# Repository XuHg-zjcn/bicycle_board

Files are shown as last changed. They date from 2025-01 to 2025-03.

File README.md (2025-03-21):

# 自行车主控板

## 前系统特征
### 板载资源
- ESP32-C3-WROOM-2U, xx32F103C8T6
- 太阳能Buck降压电路，可用MPPT驱动
- USB 5V输出升压电路(PS7516)
- USB充电电路(TP4056)
- 数字功放(NS4168)
- 2路NMOS(可连接车灯、报警器)
- IMU传感器(QMI8610,ICM-42688-P)
- 磁力计(QMC6308,QMC7983)
- 气压计(SPL06-001)
- 温湿度计(AHT20)
- FRAM储存器(MB85RS256B)

### 接口
- 8PIN SPI显示屏接口
- 扬声器接口
- I2S麦克风
- TF卡槽
- 3.7V锂电池接口
- 外置I2C接口(连接传感器和GPIO扩展芯片)
- 指纹传感器接口
- 后系统接口(UART)
- USB-C口(可充电,连接ESP32-C3模块)
- USB-A口(可放电,连接xx32芯片)
- 5V输出接口，用于连接USB公头
- 霍尔传感器接口x2(2个可以用于区分前进和后退)

### 待添加
- USB PD输出
- 外置电池组接口
- 转向角编码器接口
- 板载LoRa模块
- 发电机稳压电路

## 评论
前系统有一些射频发射源，GNSS模块和天线打算放在后系统附近，通过增大距离来减少干扰。  
暂时不考虑刷卡解锁，先考虑支持指纹和蓝牙  
按键，刹车开关，副车灯，风扇等电路等放在与显示屏同一块PCB中，使用PCA9555/TCA9555 GPIO扩展芯片  
为了提高稳定性，IMU和磁力计PCB上各有两个的不同封装可以焊接，只焊一个也可以。

为了减少git仓库占用空间，我在`git commit`提交前在KiCad中清除所有填充域(快捷键Ctrl+B)，您可以在打开后重新填充(快捷键B)  
在KiCad的Python控制台中，切换到该repo根目录运行下例命令
````python
import build
build.all()
```
即可自动完成添加泪滴、重新填充、应用PCB背面信息字符串

## 历史
2024.12.23 发布v1.0(第一次PCB打样)

下一个版本考虑
- 把ESP32和外围设备(microSD、音频等)等移动到显示屏附近PCB上
- 是否应该将太阳能、发电机相关电路尽可能移动到太阳能板、发电机附近

2025.2.21 发现TXB0108PW的OE端未连接，已飞线连接到+1V8

2025.3.21 发现用于光伏MPPT的DCDC不可用，Q6栅极关闭时电流会从体二极管流过

## 版权和许可证
Copyright (C) 2024 徐瑞骏

本设计以CERN开放硬件许可证第二版强互惠授权(CERN Open Hardware Licence Version 2 - Strongly Reciprocal)，许可证文件位于`LICENSE.txt`

本设计不提供任何保证

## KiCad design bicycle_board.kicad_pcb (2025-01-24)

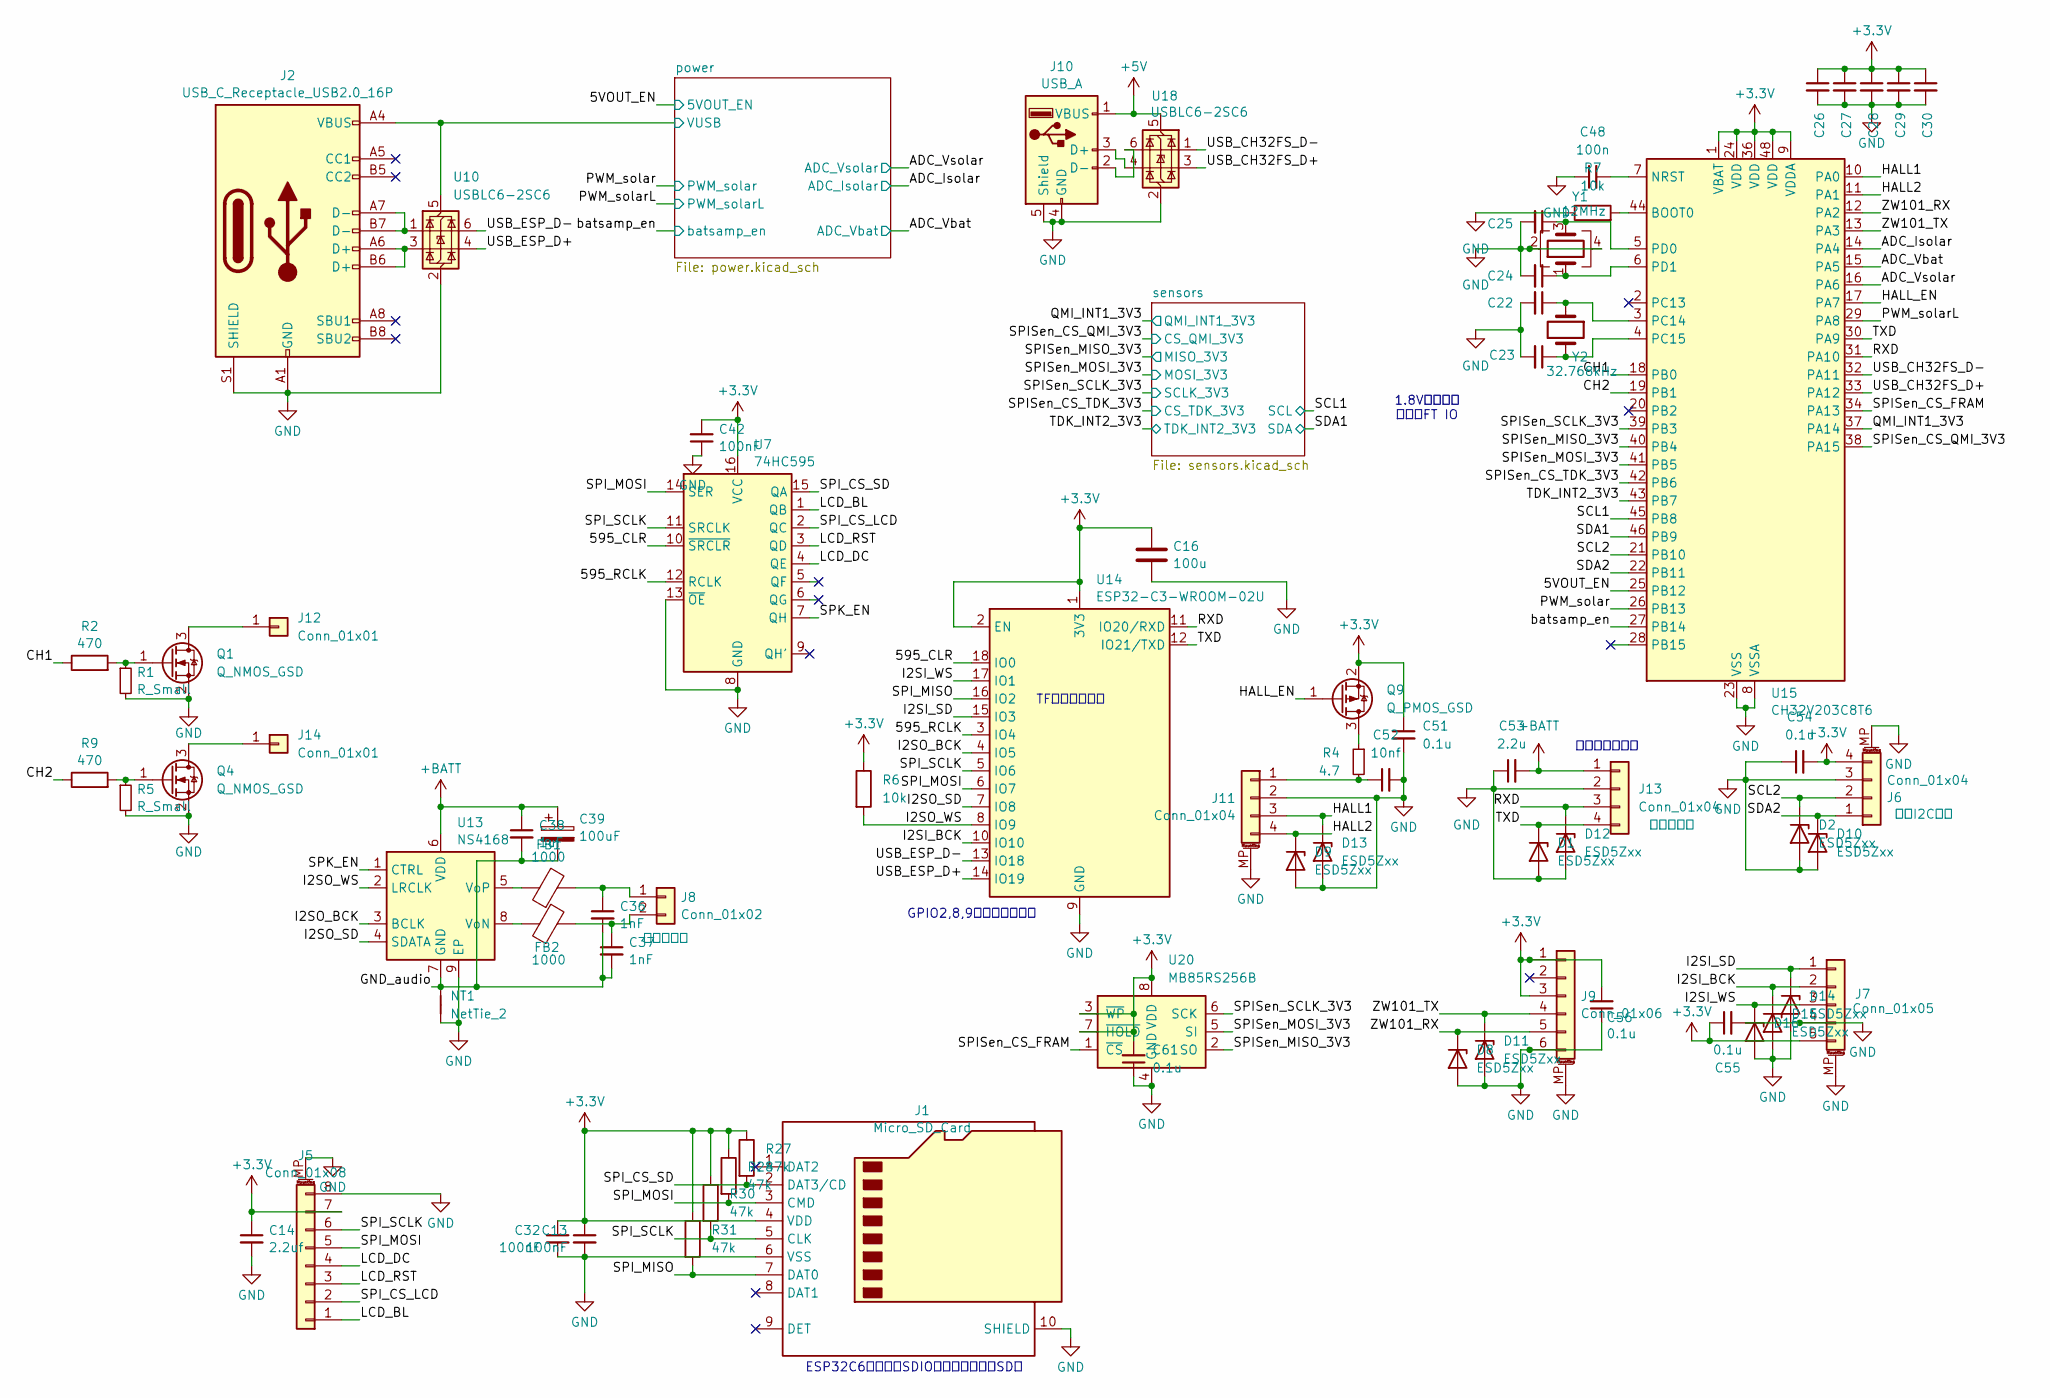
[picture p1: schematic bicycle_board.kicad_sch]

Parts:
C13, C26, C27, C28, C29, C30, C32, C42: 100nF; C_0402_1005Metric
C14: 2.2uf; C_0603_1608Metric
C16: 100u; C_1210_3225Metric
C22, C23, C24, C25: C_Small; C_0402_1005Metric
C36, C37: 1nF; C_0402_1005Metric
C38: 1uF; C_0402_1005Metric
C39: 100uF; C_1210_3225Metric
C48: 100n; C_0402_1005Metric
C51, C54, C55, C56, C61: 0.1u; C_0402_1005Metric
C52: 10nf; C_0402_1005Metric
C53: 2.2u; C_0603_1608Metric
D1, D2, D8, D9, D10, D11, D12, D13, D14, D15, D16: ESD5Zxx; D_SOD-523
FB1, FB2: 1000; L_0805_2012Metric
J1: Micro_SD_Card; microSD_Slot_mybuy
J2: USB_C_Receptacle_USB2.0_16P; USB_C_Receptacle_HRO_TYPE-C-31-M-12
J5: Conn_01x08; JST_SH_SM08B-SRSS-TB_1x08-1MP_P1.00mm_Horizontal
J6, J11: Conn_01x04; JST_SH_SM04B-SRSS-TB_1x04-1MP_P1.00mm_Horizontal
J7: Conn_01x05; JST_SH_SM05B-SRSS-TB_1x05-1MP_P1.00mm_Horizontal
J8: Conn_01x02; PinHeader_1x02_P2.54mm_Vertical
J9: Conn_01x06; JST_SH_SM06B-SRSS-TB_1x06-1MP_P1.00mm_Horizontal
J10: USB_A; USB_A_Molex_67643_Horizontal
J12, J14: Conn_01x01; TestPoint_Pad_D1.0mm
J13: Conn_01x04; PinHeader_1x04_P2.54mm_Vertical
NT1: NetTie_2; NetTie-2_SMD_Pad0.5mm
Q1, Q4: Q_NMOS_GSD; SOT-23
Q9: Q_PMOS_GSD; SOT-523
R1, R5: R_Small; R_0402_1005Metric
R2, R9: 470; R_0402_1005Metric
R4: 4.7; R_0402_1005Metric
R6, R7: 10k; R_0402_1005Metric
R27, R28, R30, R31: 47k; R_0402_1005Metric
U7: 74HC595; SSOP-16_4.4x5.2mm_P0.65mm
U10, U18: USBLC6-2SC6; SOT-23-6
U13: NS4168; HSOP-8-1EP_3.9x4.9mm_P1.27mm_EP2.3x2.3mm
U14: ESP32-C3-WROOM-02U
U15: CH32V203C8T6; LQFP-48_7x7mm_P0.5mm
U20: MB85RS256B; SSOP-8_3.9x5.05mm_P1.27mm
Y1: 12MHz; Crystal_SMD_2016-4Pin_2.0x1.6mm
Y2: 32.768kHz; Crystal_SMD_2012-2Pin_2.0x1.2mm

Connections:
+3.3V: C13.1, C14.1, C16.1, C26.1, C27.1, C28.1, C29.1, C30.1, C32.1, C42.2, C51.1, C54.2, C55.1, C56.2, C61.2, J1.4 (VDD), J5.7, J6.4, J7.5, J9.1, J9.3, Q9.2 (S), R6.1, R27.1, R28.1, R30.1, R31.1, U7.16 (VCC), U14.1 (3V3), U14.2 (EN), U15.1 (VBAT), U15.9 (VDDA), U15.24 (VDD), U15.36 (VDD), U15.48 (VDD), U20.3 (~WP), U20.7 (~HOLD), U20.8 (VDD); also elsewhere on the board
+5V: J10.1 (VBUS), U18.5 (VBUS); also elsewhere on the board
+BATT: C38.1, C39.1, C53.2, J13.1, U13.6 (VDD); also elsewhere on the board
/5VOUT_EN: U15.25 (PB12); also elsewhere on the board
/595_CLR: U7.10 (~SRCLR), U14.18 (IO0)
/595_RCLK: U7.12 (RCLK), U14.3 (IO4)
/ADC_Isolar: U15.14 (PA4); also elsewhere on the board
/ADC_Vbat: U15.15 (PA5); also elsewhere on the board
/ADC_Vsolar: U15.16 (PA6); also elsewhere on the board
/CH1: R2.1, U15.18 (PB0)
/CH2: R9.1, U15.19 (PB1)
/GND_audio: C36.2, C37.2, C38.2, C39.2, NT1.2, U13.7 (GND)
/HALL1: D13.1 (K), J11.3, U15.10 (PA0)
/HALL2: D9.1 (K), J11.4, U15.11 (PA1)
/HALL_EN: Q9.1 (G), U15.17 (PA7)
/I2SI_BCK: D15.1 (K), J7.2, U14.10 (IO10)
/I2SI_SD: D14.1 (K), J7.1, U14.15 (IO3)
/I2SI_WS: D16.1 (K), J7.3, U14.17 (IO1)
/I2SO_BCK: U13.3 (BCLK), U14.4 (IO5)
/I2SO_SD: U13.4 (SDATA), U14.7 (IO8)
/I2SO_WS: R6.2, U13.2 (LRCLK), U14.8 (IO9)
/LCD_BL: J5.1, U7.1 (QB)
/LCD_DC: J5.4, U7.4 (QE)
/LCD_RST: J5.3, U7.3 (QD)
/PWM_solar: U15.26 (PB13); also elsewhere on the board
/PWM_solarL: U15.29 (PA8); also elsewhere on the board
/QMI_INT1_3V3: U15.37 (PA14); also elsewhere on the board
/RXD: D12.1 (K), J13.3, U14.11 (IO20/RXD), U15.31 (PA10)
/SCL1: U15.45 (PB8); also elsewhere on the board
/SCL2: D2.1 (K), J6.2, U15.21 (PB10)
/SDA1: U15.46 (PB9); also elsewhere on the board
/SDA2: D10.1 (K), J6.1, U15.22 (PB11)
/SPISen_CS_FRAM: U15.34 (PA13), U20.1 (~CS)
/SPISen_CS_QMI_3V3: U15.38 (PA15); also elsewhere on the board
/SPISen_CS_TDK_3V3: U15.42 (PB6); also elsewhere on the board
/SPISen_MISO_3V3: U15.40 (PB4), U20.2 (SO); also elsewhere on the board
/SPISen_MOSI_3V3: U15.41 (PB5), U20.5 (SI); also elsewhere on the board
/SPISen_SCLK_3V3: U15.39 (PB3), U20.6 (SCK); also elsewhere on the board
/SPI_CS_LCD: J5.2, U7.2 (QC)
/SPI_CS_SD: J1.2 (DAT3/CD), R27.2, U7.15 (QA)
/SPI_MISO: J1.7 (DAT0), R31.2, U14.16 (IO2)
/SPI_MOSI: J1.3 (CMD), J5.5, R28.2, U7.14 (SER), U14.6 (IO7)
/SPI_SCLK: J1.5 (CLK), J5.6, R30.2, U7.11 (SRCLK), U14.5 (IO6)
/SPK_EN: U7.7 (QH), U13.1 (CTRL)
/TDK_INT2_3V3: U15.43 (PB7); also elsewhere on the board
/TXD: D1.1 (K), J13.4, U14.12 (IO21/TXD), U15.30 (PA9)
/USB_CH32FS_D+: U15.33 (PA12), U18.3 (I/O2)
/USB_CH32FS_D-: U15.32 (PA11), U18.1 (I/O1)
/USB_ESP_D+: U10.4 (I/O2), U14.14 (IO19)
/USB_ESP_D-: U10.6 (I/O1), U14.13 (IO18)
/ZW101_RX: D8.1 (K), J9.5, U15.12 (PA2)
/ZW101_TX: D11.1 (K), J9.4, U15.13 (PA3)
/batsamp_en: U15.27 (PB14); also elsewhere on the board
/power/VUSB: J2.A4 (VBUS), J2.A9 (VBUS), J2.B4 (VBUS), J2.B9 (VBUS), U10.5 (VBUS); also elsewhere on the board
GND: C13.2, C14.2, C16.2, C22.2, C23.2, C24.2, C25.2, C26.2, C27.2, C28.2, C29.2, C30.2, C32.2, C42.1, C48.1, C51.2, C52.2, C53.1, C54.1, C55.2, C56.1, C61.1, D1.2 (A), D2.2 (A), D8.2 (A), D9.2 (A), D10.2 (A), D11.2 (A), D12.2 (A), D13.2 (A), D14.2 (A), D15.2 (A), D16.2 (A), J1.6 (VSS), J1.10 (SHIELD), J2.A1 (GND), J2.A12 (GND), J2.B1 (GND), J2.B12 (GND), J2.S1 (SHIELD), J5.8, J5.MP (MountPin), J6.3, J6.MP (MountPin), J7.4, J7.MP (MountPin), J9.6, J9.MP (MountPin), J10.4 (GND), J10.5 (Shield), J11.2, J11.MP (MountPin), J13.2, NT1.1, Q1.2 (S), Q4.2 (S), R1.2, R5.2, R7.1, U7.8 (GND), U7.13 (~OE), U10.2 (GND), U13.9 (EP), U14.9 (GND), U14.19 (GND), U15.8 (VSSA), U15.23 (VSS), U15.35 (VSS), U15.47 (VSS), U18.2 (GND), U20.4 (GND), Y1.2, Y1.4; also elsewhere on the board
unnamed: J2.A6 (D+), J2.B6 (D+), U10.3 (I/O2)
unnamed: J2.A7 (D-), J2.B7 (D-), U10.1 (I/O1)
unnamed: C36.1, FB1.2, J8.1
unnamed: C37.1, FB2.2, J8.2
unnamed: J10.3 (D+), U18.4 (I/O2)
unnamed: J10.2 (D-), U18.6 (I/O1)
unnamed: C52.1, J11.1, R4.2
unnamed: J12.1, Q1.3 (D)
unnamed: J14.1, Q4.3 (D)
unnamed: Q1.1 (G), R1.1, R2.2
unnamed: Q4.1 (G), R5.1, R9.2
unnamed: Q9.3 (D), R4.1
unnamed: FB2.1, U13.8 (VoN)
unnamed: FB1.1, U13.5 (VoP)
unnamed: R7.2, U15.44 (BOOT0)
unnamed: C48.2, U15.7 (NRST)
unnamed: C22.1, U15.3 (PC14), Y2.1
unnamed: C23.1, U15.4 (PC15), Y2.2
unnamed: C25.1, U15.5 (PD0), Y1.3
unnamed: C24.1, U15.6 (PD1), Y1.1

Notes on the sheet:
ESP32C6只能作为SDIO从机，无法驱动SD卡
GPIO2,8,9与启动模式有关
1.8V信号输入 需接到FT IO
应该加短路保护
TF卡槽处已上拉

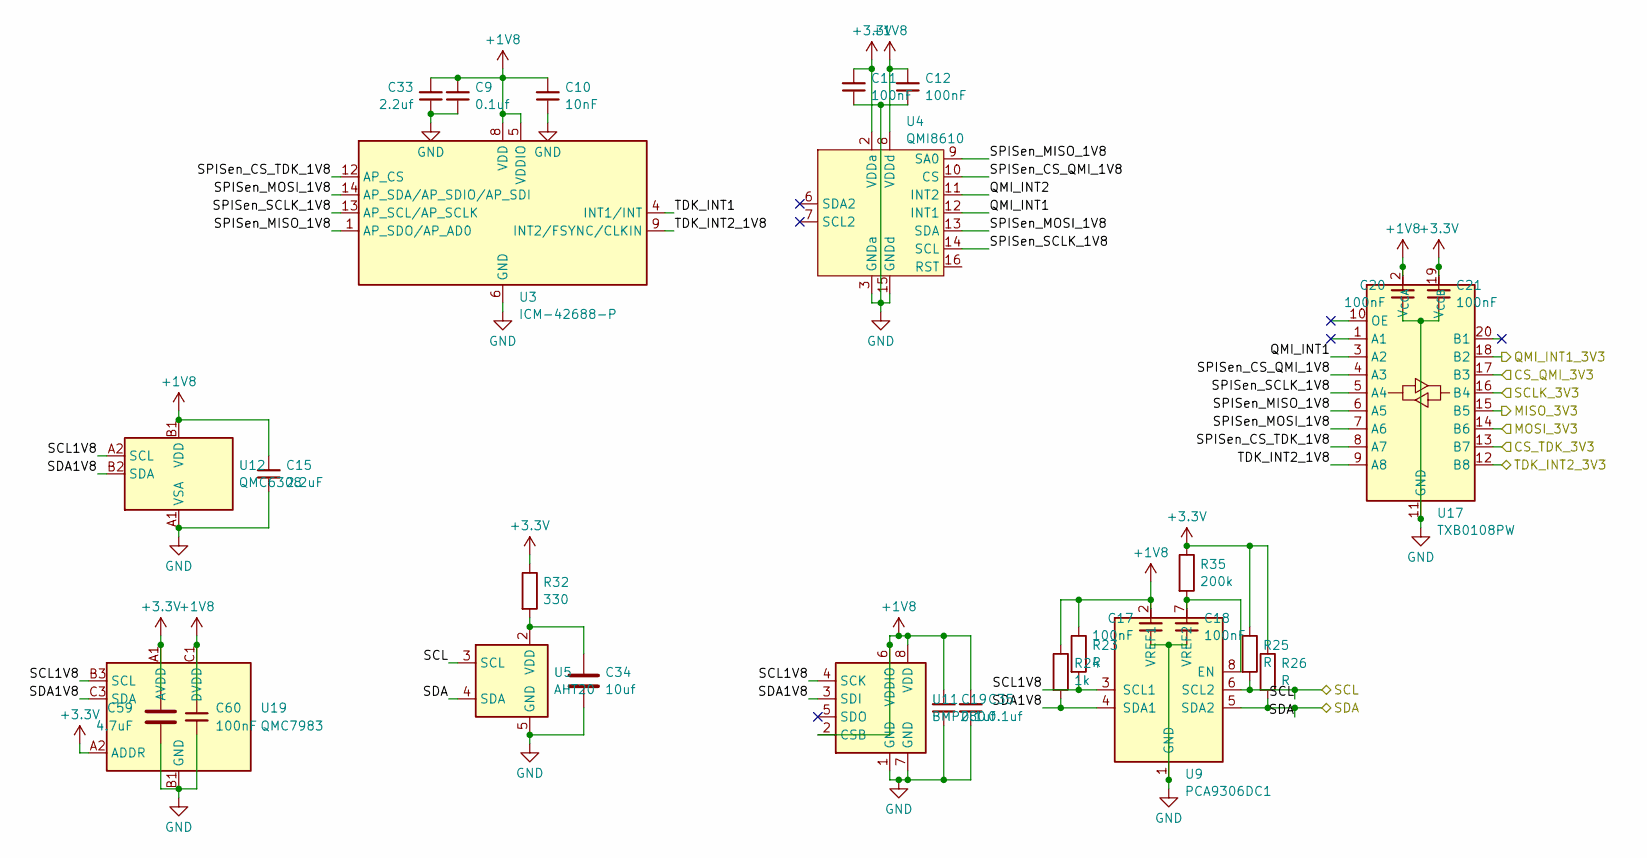
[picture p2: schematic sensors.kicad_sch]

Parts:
C9, C19, C35: 0.1uf; C_0402_1005Metric
C10: 10nF; C_0402_1005Metric
C11, C12, C17, C18, C20, C21, C60: 100nF; C_0402_1005Metric
C15: 2.2uF; C_0402_1005Metric
C33: 2.2uf; C_0603_1608Metric
C34: 10uf; C_0603_1608Metric
C59: 4.7uF; C_0603_1608Metric
R23, R25, R26: R; R_0402_1005Metric
R24: 1k; R_0402_1005Metric
R32: 330; R_0603_1608Metric
R35: 200k; R_0402_1005Metric
U3: ICM-42688-P; Bosch_LGA-14_3x2.5mm_P0.5mm
U4: QMI8610; LGA-16_3x3mm_P0.5mm
U5: AHT20; DFN-6_3x3mm_P1.0mm_AHT2x_AHT30
U9: PCA9306DC1; VSSOP-8_2.3x2mm_P0.5mm
U11: BMP280; Bosch_LGA-8_2x2.5mm_P0.65mm_ClockwisePinNumbering
U12: QMC6308; WLP-4_0.86x0.86mm_P0.4mm
U17: TXB0108PW; TSSOP-20_4.4x6.5mm_P0.65mm
U19: QMC7983; WLP-8_1.2x1.2mm_Layout3x3_P0.4mm_Pad0.24mm

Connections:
+1V8: C9.2, C10.2, C12.2, C15.2, C17.2, C19.2, C20.2, C33.2, C35.2, C60.1, R23.1, R24.1, U3.5 (VDDIO), U3.8 (VDD), U4.8 (VDDd), U9.2 (VREF1), U11.2 (CSB), U11.6 (VDDIO), U11.8 (VDD), U12.B1 (VDD), U17.2 (V_{CCA}), U19.C1 (DVDD); also elsewhere on the board
+3.3V: C11.2, C21.2, C59.1, R25.1, R26.1, R32.1, R35.1, U4.2 (VDDa), U17.19 (V_{CCB}), U19.A1 (AVDD), U19.A2 (ADDR); also elsewhere on the board
/QMI_INT1_3V3: U17.18 (B2); also elsewhere on the board
/SCL1: R25.2, U5.3 (SCL), U9.6 (SCL2); also elsewhere on the board
/SDA1: R26.2, U5.4 (SDA), U9.5 (SDA2); also elsewhere on the board
/SPISen_CS_QMI_3V3: U17.17 (B3); also elsewhere on the board
/SPISen_CS_TDK_3V3: U17.13 (B7); also elsewhere on the board
/SPISen_MISO_3V3: U17.15 (B5); also elsewhere on the board
/SPISen_MOSI_3V3: U17.14 (B6); also elsewhere on the board
/SPISen_SCLK_3V3: U17.16 (B4); also elsewhere on the board
/TDK_INT2_3V3: U17.12 (B8); also elsewhere on the board
/sensors/QMI_INT1: U4.12 (INT1), U17.3 (A2)
/sensors/QMI_INT2: U4.11 (INT2)
/sensors/SCL1V8: R23.2, U9.3 (SCL1), U11.4 (SCK), U12.A2 (SCL), U19.B3 (SCL)
/sensors/SDA1V8: R24.2, U9.4 (SDA1), U11.3 (SDI), U12.B2 (SDA), U19.C3 (SDA)
/sensors/SPISen_CS_QMI_1V8: U4.10 (CS), U17.4 (A3)
/sensors/SPISen_CS_TDK_1V8: U3.12 (AP_CS), U17.8 (A7)
/sensors/SPISen_MISO_1V8: U3.1 (AP_SDO/AP_AD0), U4.9 (SA0), U17.6 (A5)
/sensors/SPISen_MOSI_1V8: U3.14 (AP_SDA/AP_SDIO/AP_SDI), U4.13 (SDA), U17.7 (A6)
/sensors/SPISen_SCLK_1V8: U3.13 (AP_SCL/AP_SCLK), U4.14 (SCL), U17.5 (A4)
/sensors/TDK_INT1: U3.4 (INT1/INT)
/sensors/TDK_INT2_1V8: U3.9 (INT2/FSYNC/CLKIN), U17.9 (A8)
GND: C9.1, C10.1, C11.1, C12.1, C15.1, C17.1, C18.1, C19.1, C20.1, C21.1, C33.1, C34.2, C35.1, C59.2, C60.2, U3.6 (GND), U3.7 (GND), U4.3 (GNDa), U4.15 (GNDd), U5.5 (GND), U9.1 (GND), U11.1 (GND), U11.7 (GND), U12.A1 (VSA), U17.11 (GND), U19.B1 (GND); also elsewhere on the board
unnamed: C34.1, R32.2, U5.2 (VDD)
unnamed: C18.2, R35.2, U9.7 (VREF2), U9.8 (EN)

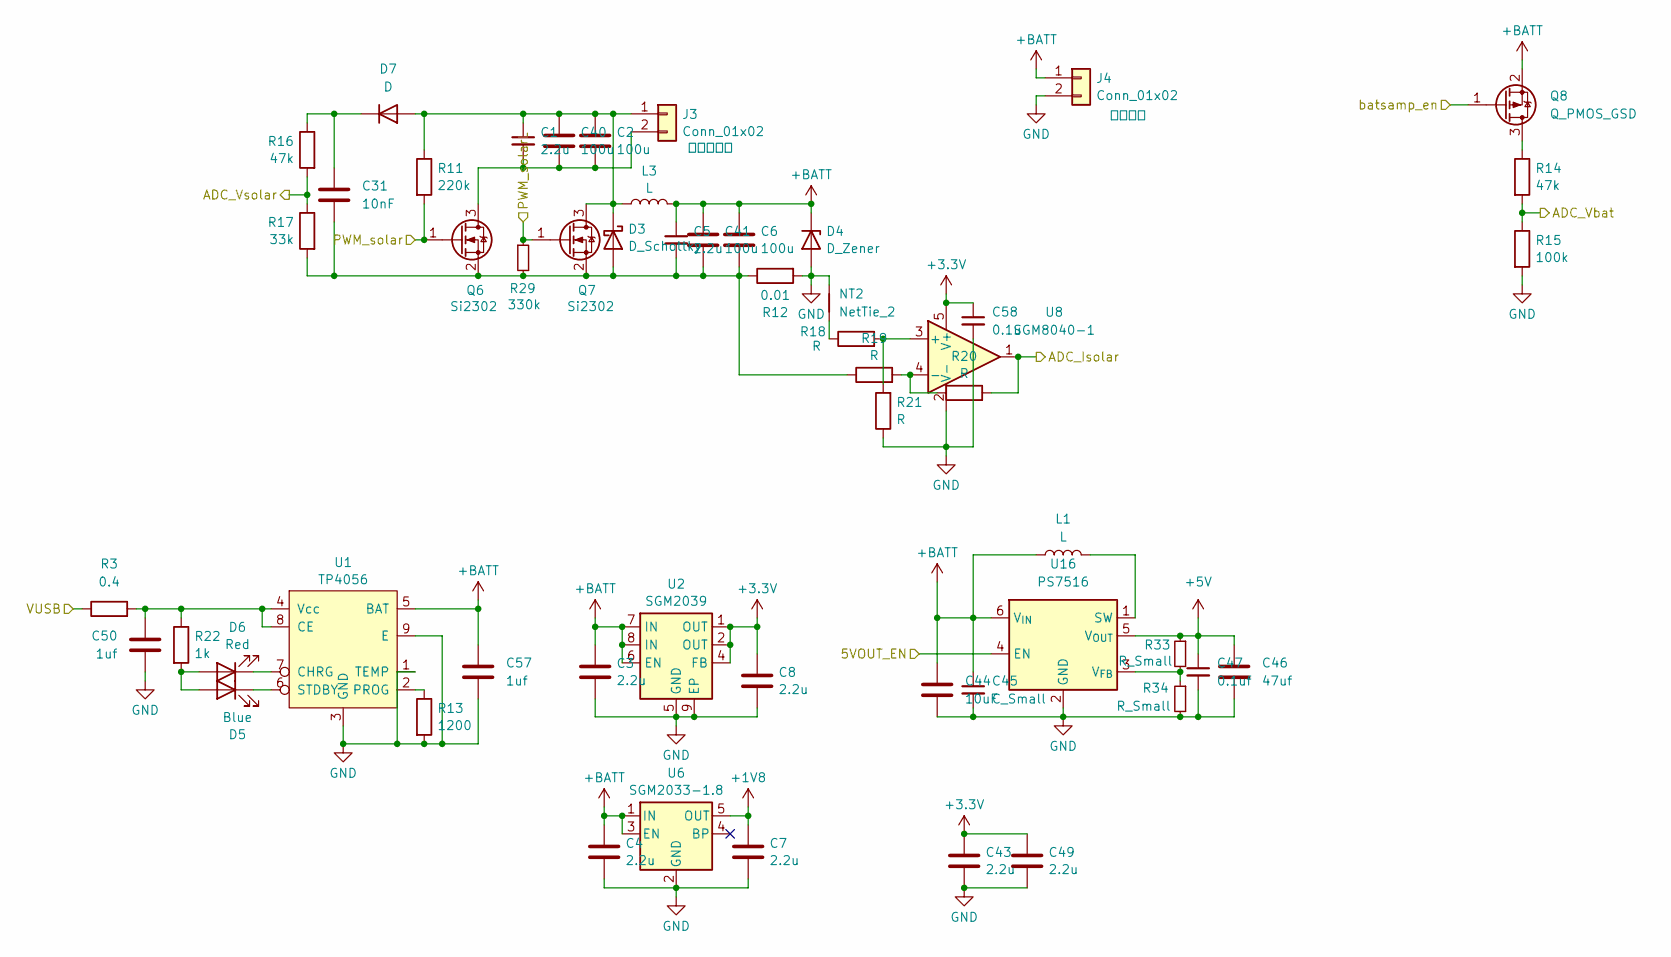
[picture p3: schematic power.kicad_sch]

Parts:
C1, C3, C4, C5, C7, C8: 2.2u; C_0805_2012Metric
C2, C6, C40, C41: 100u; C_1210_3225Metric
C31: 10nF; C_0402_1005Metric
C43, C49: 2.2u; C_0603_1608Metric
C44: 10uF; C_0805_2012Metric
C45: C_Small; C_0402_1005Metric
C46: 47uf; C_1210_3225Metric
C47: 0.1uf; C_0402_1005Metric
C50, C57: 1uf; C_0603_1608Metric
C58: 0.1u; C_0402_1005Metric
D3: D_Schottky; D_SOD-123F
D4: D_Zener; D_SOD-123F
D5: Blue; LED_0603_1608Metric
D6: Red; LED_0603_1608Metric
D7: D; D_SOD-323
J3, J4: Conn_01x02; PinHeader_1x02_P2.54mm_Vertical
L1, L3: L; L_6.3x6.3_H3
NT2: NetTie_2; NetTie-2_SMD_Pad0.5mm
Q6, Q7: Si2302; SOT-23
Q8: Q_PMOS_GSD; SOT-23
R3: 0.4; R_1206_3216Metric
R11: 220k; R_0402_1005Metric
R12: 0.01; R_1206_3216Metric
R13: 1200; R_0402_1005Metric
R14, R16: 47k; R_0402_1005Metric
R15: 100k; R_0402_1005Metric
R17: 33k; R_0402_1005Metric
R18, R19, R20, R21: R; R_0402_1005Metric
R22: 1k; R_0402_1005Metric
R29: 330k; R_0402_1005Metric
R33, R34: R_Small; R_0402_1005Metric
U1: TP4056; HTSOP-8-1EP_3.9x4.9mm_P1.27mm_EP2.4x3.2mm_ThermalVias
U2: SGM2039; DFN-8-1EP_1.2x1.6mm_P0.4mm_EP0.3x1.3mm
U6: SGM2033-1.8; SOT-23-5
U8: SGM8040-1; SOT-23-5
U16: PS7516; SOT-23-6

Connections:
+1V8: C7.1, U6.5 (OUT); also elsewhere on the board
+3.3V: C8.1, C43.1, C49.1, C58.1, U2.1 (OUT), U2.2 (OUT), U2.4 (FB), U8.5 (V+); also elsewhere on the board
+5V: C46.1, C47.1, R33.1, U16.5 (V_{OUT}); also elsewhere on the board
+BATT: C3.1, C4.1, C5.1, C6.1, C41.1, C44.1, C45.1, C57.1, D4.1 (K), J4.1, L1.1, L3.2, Q8.2 (S), U1.5 (BAT), U2.6 (EN), U2.7 (IN), U2.8 (IN), U6.1 (IN), U6.3 (EN), U16.6 (V_{IN}); also elsewhere on the board
/5VOUT_EN: U16.4 (EN); also elsewhere on the board
/ADC_Isolar: R20.2, U8.1; also elsewhere on the board
/ADC_Vbat: R14.2, R15.1; also elsewhere on the board
/ADC_Vsolar: R16.2, R17.1; also elsewhere on the board
/PWM_solar: Q6.1 (G), R11.2; also elsewhere on the board
/PWM_solarL: Q7.1 (G), R29.1; also elsewhere on the board
/batsamp_en: Q8.1 (G); also elsewhere on the board
/power/VUSB: R3.1; also elsewhere on the board
GND: C3.2, C4.2, C7.2, C8.2, C43.2, C44.2, C45.2, C46.2, C47.2, C49.2, C50.2, C57.2, C58.2, D4.2 (A), J4.2, NT2.2, R12.2, R13.2, R15.2, R21.1, R34.2, U1.1 (TEMP), U1.3 (GND), U1.9 (E), U2.5 (GND), U2.9 (EP), U6.2 (GND), U8.2 (V-), U16.2 (GND); also elsewhere on the board
unnamed: C5.2, C6.2, C31.2, C41.2, D3.2 (A), Q6.2 (S), Q7.2 (S), R12.1, R17.2, R19.1, R29.2
unnamed: C1.1, C2.1, C40.1, D3.1 (K), D7.2 (A), J3.1, L3.1, Q7.3 (D), R11.1
unnamed: D5.2 (A), D6.2 (A), R22.2
unnamed: D5.1 (K), U1.6 (STDBY)
unnamed: D6.1 (K), U1.7 (CHRG)
unnamed: C31.1, D7.1 (K), R16.1
unnamed: C1.2, C2.2, C40.2, J3.2, Q6.3 (D)
unnamed: NT2.1, R18.1
unnamed: Q8.3 (D), R14.1
unnamed: C50.1, R3.2, R22.1, U1.4 (Vcc), U1.8 (CE)
unnamed: R13.1, U1.2 (PROG)
unnamed: R18.2, R21.2, U8.3 (+)
unnamed: R19.2, R20.1, U8.4 (-)
unnamed: L1.2, U16.1 (SW)
unnamed: R33.2, R34.1, U16.3 (V_{FB})

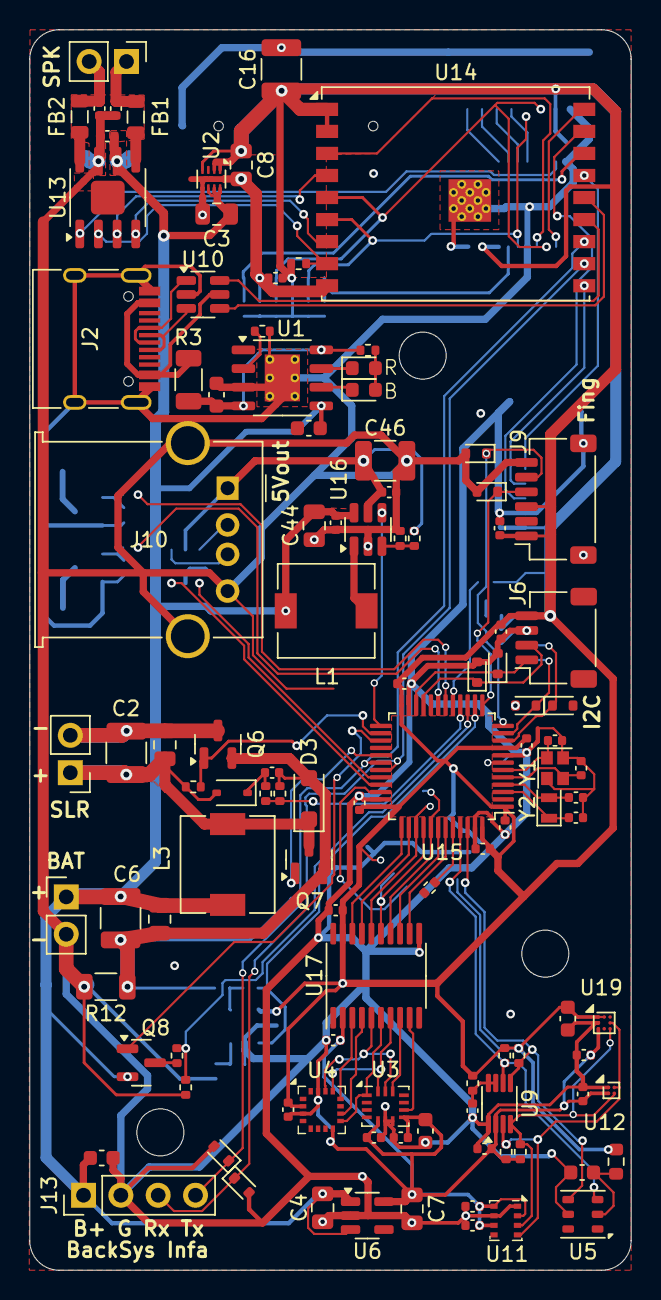
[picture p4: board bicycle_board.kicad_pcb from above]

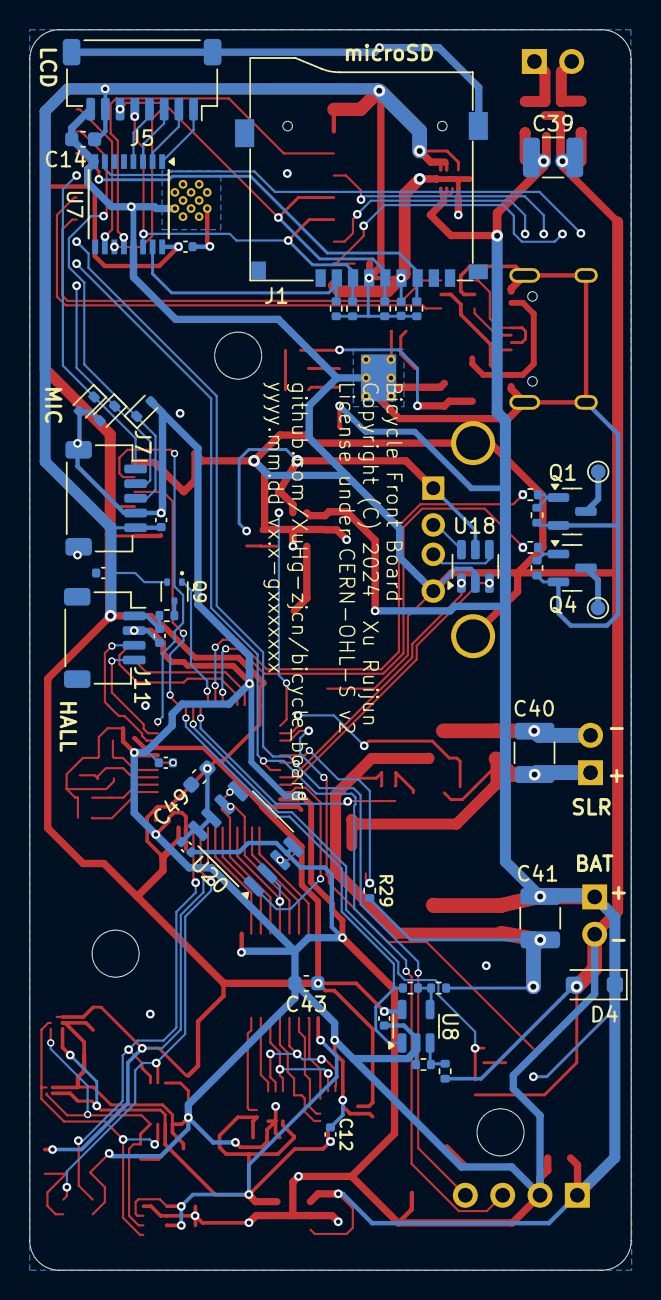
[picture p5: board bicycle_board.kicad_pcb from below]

Board: 2 copper layers, 40.9 x 84.4 mm, 158 parts (47 on the bottom side), 102 nets.

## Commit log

2024-11-18 MOS管修改为GSD, 添加芯片附近滤波电容、上拉电阻等，调整模块间布局，改正AHT20封装，电解电容替换成1210 MLCC
    [bicycle_board.kicad_pcb, bicycle_board.kicad_sch, power.kicad_sch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]
2024-11-18 添加升压USB 5V输出
    [bicycle_board.kicad_pcb, bicycle_board.kicad_sch, power.kicad_sch]
2024-11-18 PCB上元器件分组
    [bicycle_board.kicad_pcb]
2024-11-18 初步划定PCB边缘，改为紧凑布局
    [bicycle_board.kicad_pcb, bicycle_board.kicad_sch]
2024-11-19 收窄PCB宽度到47.4mm
    [bicycle_board.kicad_pcb, bicycle_board.kicad_sch]
2024-11-19 画我现有的SD卡槽封装，应用到PCB
    [bicycle_board.kicad_pcb, bicycle_board.kicad_sch]
2024-11-20 PCB宽度进一步收缩到41.4mm，晶振改2016和2012，最小线距改0.15mm，添加一些布线
    [bicycle_board.kicad_pcb, bicycle_board.kicad_sch]
2024-11-22 添加CERN-OHL-S许可证、README.md文件
    [bicycle_board.kicad_pcb]
2024-12-01 连接大多数布线，做一些调整，添加覆铜
    [bicycle_board.kicad_pcb, bicycle_board.kicad_sch, sensors.kicad_sch]
2024-12-01 移除第二个74HC595，SGM2033-1.8改成一直开启，按PCA9306数据手册修改供电
    [bicycle_board.kicad_pcb, bicycle_board.kicad_sch, power.kicad_sch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]
2024-12-01 修改小孔径为0.25/0.5mm
    [bicycle_board.kicad_pcb]
2024-12-01 修复一些DRC错误和警告，大多数信号接口改成SH1.0接口
    [bicycle_board.kicad_pcb, bicycle_board.kicad_sch]
2024-12-04 添加霍尔元件接口，移除CH2,CH3 MOS通道，调整和连接布线，取消STM32与ESP32的SPI连接
    [bicycle_board.kicad_pcb, bicycle_board.kicad_sch]
2024-12-05 调整STM32 GPIO使用，移除右侧MOS通道，只在左侧底部保留2个，计划采用PCA9555/TCA9555 GPIO扩展芯片
    [bicycle_board.kicad_pcb, bicycle_board.kicad_sch]
2024-12-05 连接ESP32和I2S麦克风接口
    [bicycle_board.kicad_pcb, bicycle_board.kicad_sch]
2024-12-05 调整电源线宽度，一些走线布局
    [bicycle_board.kicad_pcb, bicycle_board.kicad_sch, power.kicad_sch]
2024-12-09 接口添加TVS二极管和去耦电容，调整已有电容连接走线宽度
    [bicycle_board.kicad_pcb, bicycle_board.kicad_sch, power.kicad_sch]
2024-12-09 I2S麦克风接口添加TVS管
    [bicycle_board.kicad_pcb, bicycle_board.kicad_sch]
2024-12-09 添加3个机械孔
    [bicycle_board.kicad_pcb]
2024-12-11 微调元器件布局和走线，适当增大TXD与RXD，SCL1与SDA1走线间距
    [bicycle_board.kicad_pcb]
2024-12-11 整理分组：添加缺失的成员，新建一些分组，给分组命名
    [bicycle_board.kicad_pcb]
2024-12-12 修复和排除一些DRC错误
    [bicycle_board.kicad_pcb]
2024-12-12 整理和添加一些接口丝印和背面信息文本
    [bicycle_board.kicad_pcb]
2024-12-13 改进电源走线，添加小面积覆铜；添加USB-A接口背面MOS管位号
    [bicycle_board.kicad_pcb]
2024-12-13 移动和微调MOS管通道电路并添加外接电路焊盘
    [bicycle_board.kicad_pcb, bicycle_board.kicad_sch]
2024-12-13 更新README.md
2024-12-13 调整启动相关GPIO，ESO32添加GPIO9上拉电阻；STM32 BOOT0添加下拉电阻
    [bicycle_board.kicad_pcb, bicycle_board.kicad_sch]
2024-12-16 最小孔径增加到0.3mm，便于在大多数PCB工厂打样时降低成本
    [bicycle_board.kicad_pcb]
2024-12-16 大电流过孔扩大到0.4/0.8mm，调整过孔位置
    [bicycle_board.kicad_pcb]
2024-12-16 工程中修改为正确芯片型号QMC6308,ICM-42688-P，按数据手册更新供电滤波电容值
    [bicycle_board.kicad_pcb, sensors.kicad_sch]
2024-12-16 添加第二个磁力计QMC7983
    [bicycle_board.kicad_pcb, sensors.kicad_sch]
2024-12-18 添加build.py脚本，更新README.md和.gitignore文件
2024-12-18 按数据手册调整NS4168布线，电源GND改用单点连接，加粗电源和喇叭走线到0.6mm，中心焊盘连接GND增强散热性能
    [bicycle_board.kicad_pcb, bicycle_board.kicad_sch]
2024-12-18 调整电源走线，ESP32左侧添加3.3V覆铜
    [bicycle_board.kicad_pcb]
2024-12-18 修复一些ERC错误
    [bicycle_board.kicad_sch, power.kicad_sch, sensors.kicad_sch]
2024-12-18 GND布线，检查回路完整性
    [bicycle_board.kicad_pcb]
2024-12-18 太阳能充电电流测量GND回路用NetTie分割为不同的网络，避免被覆铜覆盖
    [bicycle_board.kicad_pcb, power.kicad_sch]
2024-12-20 添加FRAM储存器
    [bicycle_board.kicad_pcb, bicycle_board.kicad_sch]
2024-12-22 README添加待添加发电机电路记录，写下一些下一个版本的计划
2024-12-23 TP4056散热焊盘改用实心连接
    [bicycle_board.kicad_pcb]
2024-12-23 PCB边缘改半径2mm圆角，移动一些丝印避免与边缘过近
    [bicycle_board.kicad_pcb]
2024-12-23 发布v1.0
2024-12-27 fix: 根据PCB厂商EQ问题修复SGM2309的散热焊盘，添加到F.Mask层
    [bicycle_board.kicad_pcb]
2024-12-27 调整位号和文本丝印，恢复有用的被隐藏丝印，添加和优化一些文字
    [bicycle_board.kicad_pcb, power.kicad_sch]
2025-01-24 修复R12封装错误，1210电容改为1206电阻
    [bicycle_board.kicad_pcb, power.kicad_sch]
2025-03-21 doc: README中添加PCB设计缺陷描述

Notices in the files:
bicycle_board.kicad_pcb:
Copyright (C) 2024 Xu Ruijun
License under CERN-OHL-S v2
